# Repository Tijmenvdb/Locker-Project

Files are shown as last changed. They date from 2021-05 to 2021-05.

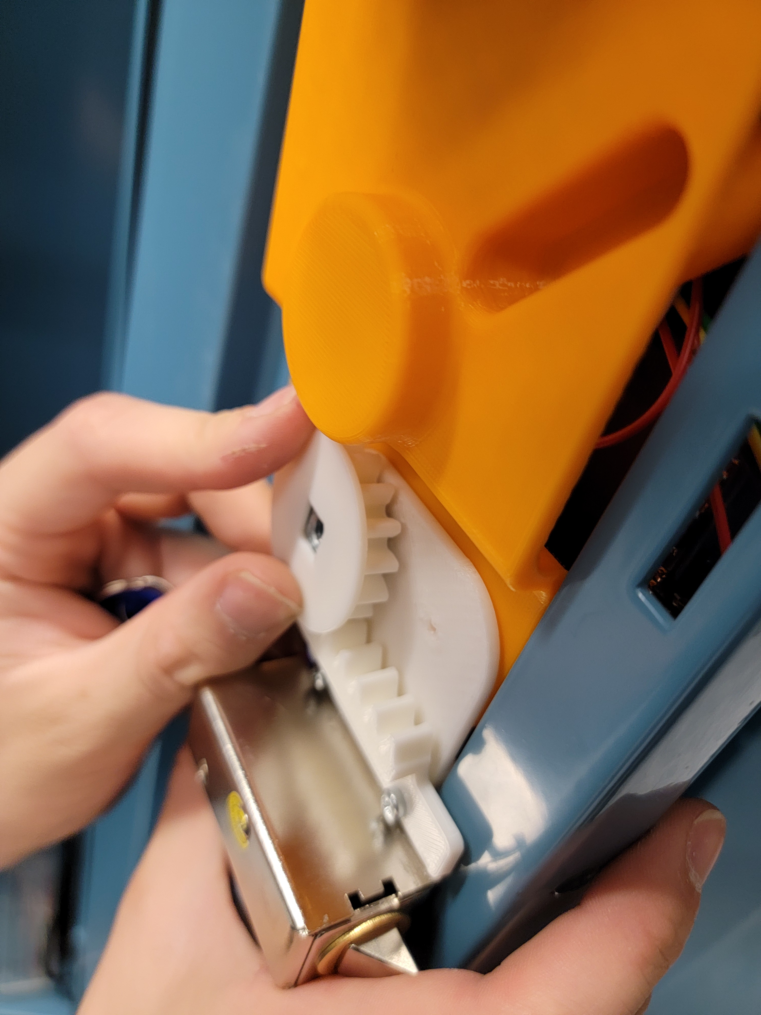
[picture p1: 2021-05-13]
CSE453 Project/Locker Documentation/Images/Assembly Pictures/20210508_183917.jpg

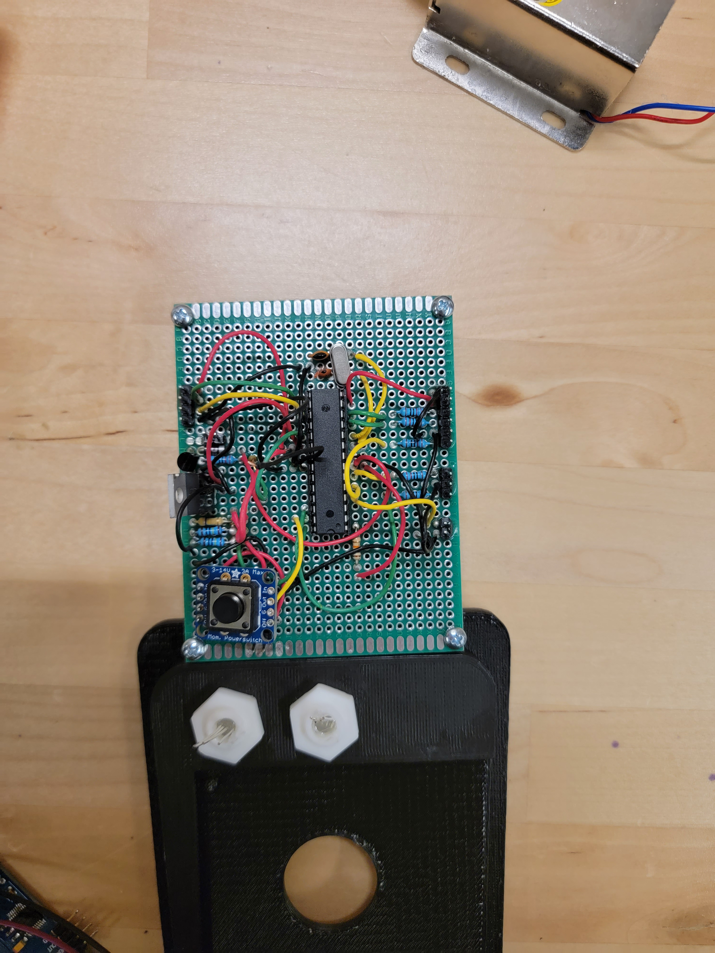
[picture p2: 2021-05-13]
CSE453 Project/Locker Documentation/Images/Assembly Pictures/20210508_151816.jpg

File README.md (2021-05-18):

# Locker-Project
We created three lockers, two for Depew Middle school and one for Alden High school. The Depew lockers we created for kids who have trouble opening up there lockers. The Alden Locker is a prototype locker for there school. We used the same hardware design for all the lockers and different code between Depew and Alden because they had different needs.

The Depew High School locker project focuses on customized lockers for individuals with physical disability. According to the needs of the client, each lock has to be designed specifically for each user to solve their problem with accessing the locker independently. Our locker is to help a student with physical or visual impairments so that they can operate the lockers without any trouble.

The Alden locker was designed as an automated and easily operated locker for Alden High School. According to the staff at Alden High School, the current lockers have frequent locker jams. This results in additional custodial resources which can be prevented by having better designed lockers.

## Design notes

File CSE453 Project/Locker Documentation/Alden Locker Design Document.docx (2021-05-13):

Automated Locker

Design Document

Prepared for:

Alden High School

Prepared By:

Tijmen Van Der Beek, Miren Patel, Siquan Wang, Xiaoang Zhang, Dazhou Liu

School of Engineering and Applied Sciences

University at Buffalo, The State University of New York

Spring 2021

Table of Contents

Introduction 2

Note for RFID and NFC Components 2

RFID Locker Module 2

Software 2

Important Static Variables 3

Functions 3

Interrupts 3

Main Flow Chart 4

RGB LED Indicator Key 5

Status LED (LEFT) 5

Battery LED (RIGHT) 6

Schematic 7

Description 7

Parts List 8

Case 9

Front 9

Inside Front 9

Back 10

Inside Back 11

Mechanical Design 11

Upgrades 12

Troubleshooting 12

References 13

# Introduction

The purpose of this project is to design an automated and easily operated locker for Alden High School. According to the staff at Alden High School, the current lockers have frequent locker jams. This results in additional custodial resources which can be prevented by having better designed lockers. These RFID Locker Modules will use Radio Frequency Identification (RFID) for authentication for opening the lockers by both registered students as well as administrative personnel such as the custodial staff. The design will also ensure that the lock mechanism does not have frequent locker jams. For the safety and security of the school, a mechanical override system will also be incorporated to allow for the circumvention of the digital systems. Due to the potential for a large rollout of this system, scalability and reliability have been key considerations at every step of our development. Everything can be found on Github (https://github.com/Tijmenvdb/Locker-Project).

# Note for RFID and NFC Components

The locking/unlocking mechanism is executed by RFID components in our design. However, the previous locker team working on Alden High School locker chose to use the NFC components. In the spring 2021 semester, we acquired the NFC components and attempted to implement them. The result was that the NFC components did not work as expected due to improper factory functionalities. As a consequence, we decided to use RFID modules to lock/unlock the locker in Alden High School.

# RFID Locker Module

1. Master tag: Acts as a master key, allowing opening the lock mechanism on any locker.
2. Registrar tag: Puts the locker into registration mode, allowing for registration of a new student tag. Student tag registrations persist until cleared with the clear tag.
3. Clear tag: Clears all registered student tags. Only master tags can open the locker until a new student tag is registered.
4. Reset Button: When the locker is first booted up you can register the administrative tags after that the reset button is the only way to reset the locker and re-register new ones.

The use of administrative tags in this way eliminates the need for additional input channels (such as buttons), reducing the hardware complexity and cost. We have also attempted to minimize the number of output channels as well, using a single RGB LED to convey the system state.

# Software

The provided RFID Locker Module software is written in C++ for deployment on an Arduino Uno (or equivalent). The main source code is LockerCodeAlden.ino. In the source code (available on our Github (https://github.com/Tijmenvdb/Locker-Project) repository) you’ll find descriptive comments to help with understanding the code’s functionality as well as its deployment.

## Important Static Variables

- Init_num: This is the number it checks to see if it has been initialized yet.
- tagDelay: This is the processing delay between each tag read in ms
- ERRORBlinkRate: This is the speed at which the led binks in ms
- LOCKER_TIME: 30 This is the time the locker has till it turns off in sec when locked
- UNLOCK_TIME: 10 This is the time the locker will be unlocked for in sec when unlocked

## Functions

- void ReadSerial(String &ReadTagString): This function reads the tag in front of the RFID sensor and passes the string through ReadTagString
- void clearTags(): This function clears all the student tags in EEPROM
- void resetLocker(): Resets the locker
- void loadTags(): This function loads all the tags from the EEPROM into the global tag_list
- bool writeTag(String data): This function adds a tag to memory and returns true if successful and false if reached max tags
- int checkTag(String data): Checks the given tag with the registered tags if any of them match it returns int for the type of tag.
- void setLed (int rVal, int gVal, int bVal): Sets the rgb led color of only the status LED
- void ledBlink (int rVal, int gVal, int bVal, int halfCycle, int blinkCount): Blink the RGB LED given the provided RGB value, the time for each half cycle (time off, time on, in ms) and the number of blinks. (Only Status LED)
- void soundFeedback(int type): Adds sound effects to the locker for better feedback (0 start, 1 unlock, 2 wrong tag)
- void initLocker(): Initializes the locker with faculty tags only runs if not initialized
- void setBatteryLed(): Sets the battery led color based on the voltage of the battery
- void enableTimerInterrupt(): Sets the timer interrupt to interrupt every second (We have a counter to determine the time)
- void resetTimer(): Resets the timer counter back to Locker_Time whenever called

## Interrupts

- void resetISR(): Sets reset to true and sets led to purple
- ISR(TIMER1_COMPA_vect): Turns off locker after timer interrupt activates and counter is at 0

# Main Flow Chart

This is a flow chart of the logic that the locker should follow.

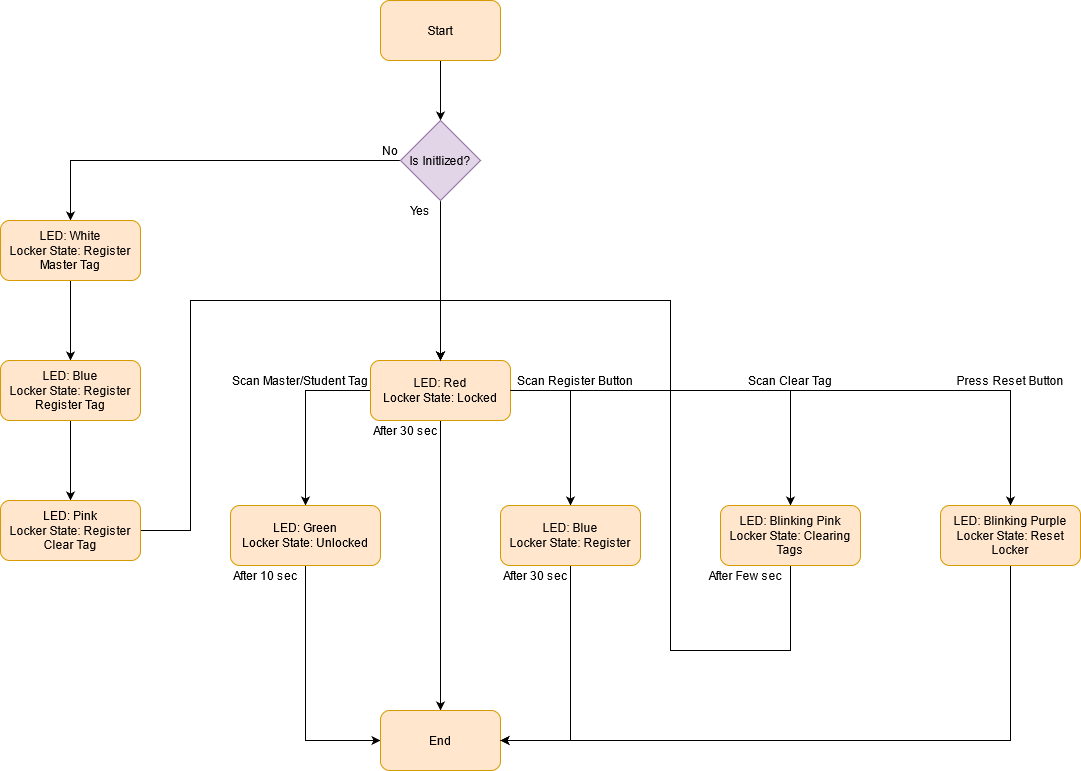
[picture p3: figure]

# RGB LED Indicator Key

## Status LED (LEFT)

State | LED Color
Initial State | OFF
Locked | RED
Unlocked | Green
Processing | Yellow
Register Mode | Blue
If the tag is wrong | Blinks RED
If the tag is correct | Blinks GREEN
Successful Register | Blinks Blue Twice
Already Registered | Blinks Blue Three Times
Unsuccessful Register | Blinks Red
Already Registered Faculty Tag | Blinks Red and color of tag type.
Resets Locker | Blinks Purple turns off
Master Tag Registration Mode | White
Register Tag Registration Mode (Only after Master Tag Reg) | Blue
Clear Tag Registration Mode | Pink
Successful Faculty Tag Registration | Blinks Color of tag type

## Battery LED (RIGHT)

State | LED 2 Color Battery Indicator LED
Initial State | OFF
When the push button is pressed, it turns on the circuit and is ready to read the tags. | GREEN: if the battery level is sufficient (battery is greater than 10 V) RED: if the battery is at low level (the battery is less than 8 V but greater than 7 V) Blinking RED: if the battery is low (the battery is less than 7 V). At this point the circuit won’t turn on, battery recharge is necessary
OFF State | OFF

# Schematic

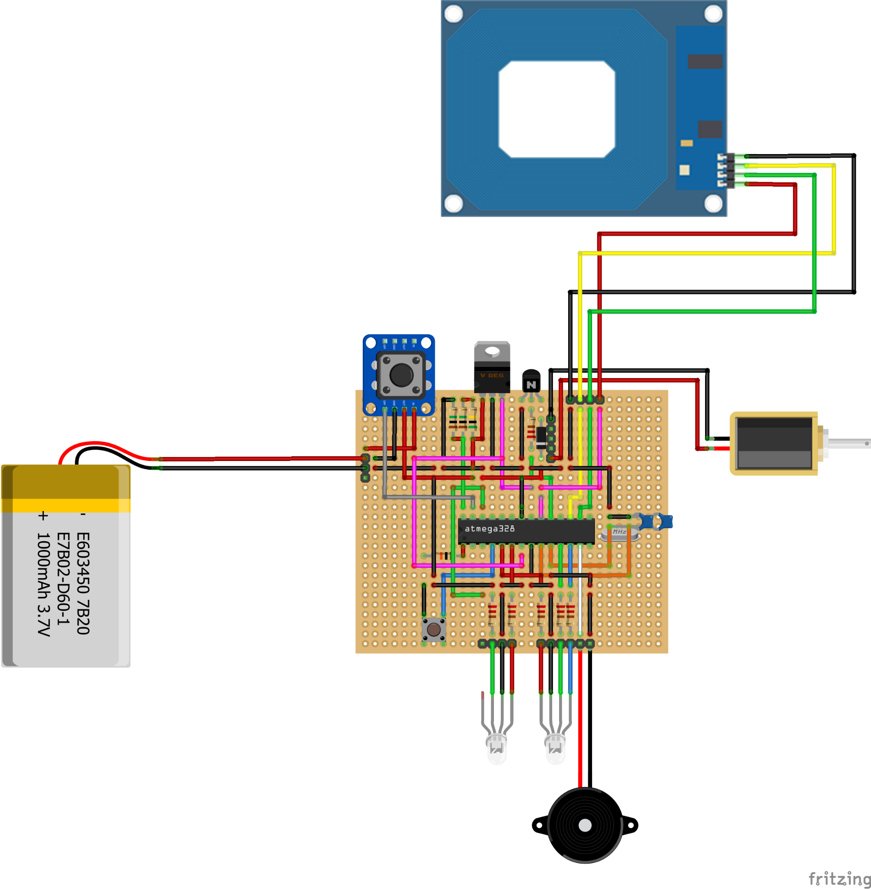
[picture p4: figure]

## Description

- We are using the atmega328p Chip that we program with the arduino and put on our circuit.
- The battery is a 12 3Ah Dewalt battery. The one in the schematic is a placeholder image.
- Adafruit Power Switch Button: This is the power button for the locker with an off pin on it allowing us to turn off the locker after being idle for a certain amount of time.
- The voltage divider takes the 12 volt power line and reduces it so the chip can read it and set the Power Led appropriately. The voltage divider consists of two 1M Ohms, one 470k Ohm and the output voltage shouldn’t exceed 5 volts.
- The Voltage regulator brings down the 12 volt to 5 volt to power the chip and RFID reader.
- The 2N2222 Transistor is used to power the solenoid with the chip.
- Status RGB LED:
  - Red On, but locked
  - Green→ Unlocked
  - Blue→ Register mode
  - Blinking pink→ Clearing all tags
  - Blinking blue→ Successful tag registration
- Power RGB LED:
  - Red Low Battery
  - Green High Battery
  - Blinking Red Out of Power
- We are using headers on the circuit board so parts can be easily replaced.
- We are using 2 22pF capacitors and a 16Mz Clock to run the chip.
- We have a 10k Ohm resistor on the reset pin on the chip.
- The resistors on the LEDs and 2N2222 transistor are 220 Ohms.

# Parts List

1. Arduino UNO R3 (https://www.mouser.com/ProductDetail/Arduino/A000066?qs=BC3YYPaifMrIue9b%252BHtKQg%3D%3D)
2. Atmega328 chips (https://www.mouser.com/ProductDetail/Microchip-Technology-Atmel/ATMEGA328P-PU?qs=K8BHR703ZXguOQv3sKbWcg%3D%3D) (Remove from Arduino board) (https://www.mouser.com/ProductDetail/Microchip-Technology-Atmel/ATMEGA328P-PU?qs=K8BHR703ZXguOQv3sKbWcg%3D%3D)
3. Adafruit Push-button Power Switch Breakout (https://www.adafruit.com/product/1400)
4. RFID Card Reader - Serial (https://www.mouser.com/ProductDetail/Parallax/28140?qs=sGAEpiMZZMuVJC7Vq%252BMl5ylqeJ96bWxk)
5. RFID Tags (https://www.mouser.com/ProductDetail/Parallax/28161?qs=6siQ5y5nVCyh2S897wNmIQ%3D%3D) x5
6. Diode Rectifier 1N4001 (https://www.sparkfun.com/products/8589) x3
7. Voltage Regulator (https://www.mouser.com/ProductDetail/STMicroelectronics/L7805ABV?qs=xv3lWMc77RfDowMbrj6NxQ%3D%3D&mgh=1)
8. 2N2222A Transistor (https://www.amazon.com/gp/product/B083TNXLHD/ref=ppx_yo_dt_b_asin_title_o08_s00?ie=UTF8&psc=1) x3
9. LED RGB Diffused (https://www.mouser.com/ProductDetail/Kingbright/WP154A4SEJ3VBDZGW-CA?qs=YCa%2FAAYMW01xRqZww6UuiQ%3D%3D) x6
10. 220ohm Resistor (https://www.amazon.com/McIgIcM-resistor-Electronics-resistors-assortment/dp/B06WRQS97C?hvadid=312303208923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) x20
11. 1M ohm Resistor (https://www.amazon.com/McIgIcM-resistor-Electronics-resistors-assortment/dp/B06WRQS97C?hvadid=312303208923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) x2
12. 470k ohm Resistor (https://www.amazon.com/McIgIcM-resistor-Electronics-resistors-assortment/dp/B06WRQS97C?hvadid=312303208923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) x
13. 10k Resistor (https://www.amazon.com/McIgIcM-resistor-Electronics-resistors-assortment/dp/B06WRQS97C?hvadid=312303208923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)
14. 22pf Capacitors (https://www.amazon.com/gp/product/B08LK8DQKF/ref=ppx_yo_dt_b_asin_title_o03_s00?ie=UTF8&psc=1) x2
15. 16Mz Clock (https://www.amazon.com/Uxcell-a14050500ux0216-HC-49S-Crystal-Oscillator/dp/B00NQ82OM0?s=industrial)
16. DeWalt 12v Lithium Ion Battery (https://www.lowes.com/pd/DEWALT-12-Volt-Max-3-Amp-Hours-Lithium-Power-Tool-Battery/1001001766?AID=11554726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)
17. DeWalt 12v-20v Lithium Ion Battery Charger (https://www.amazon.com/dp/B01BQM1A2W?ascsubtag=wtbs_5de7f7eb958a7501630f809d&m=ATVPDKIKX0DER)
18. 5V 2 Terminals Buzzer (https://www.amazon.com/gp/product/B01GJLE5BS/ref=ppx_yo_dt_b_asin_title_o02_s00?ie=UTF8&psc=1) x2
19. Key Lock (https://www.amazon.com/Prime-Line-Products-9945-Drawer-Cabinet/dp/B000BDB686)
20. Solenoid (https://www.mouser.com/ProductDetail/Adafruit/1512/)
21. PCBs (https://www.amazon.com/gp/product/B07FK49T55/ref=ppx_yo_dt_b_asin_title_o05_s00?ie=UTF8&psc=1)
22. White Filament (https://www.amazon.com/gp/product/B06XR7621X/ref=ppx_yo_dt_b_asin_title_o01_s00?ie=UTF8&psc=1) (Used for LED caps)
23. Breadboard, wiring, washers/nuts/screws
24. Push Button (https://www.amazon.com/EG-STARTS-Illuminated-Buttons-Raspberry/dp/B01N11BDX9) (Activation)
25. Push Button (https://www.amazon.com/DAOKI-Miniature-Momentary-Tactile-Quality/dp/B01CGMP9GY) (Reset)
26. Magnetic Push Latches (https://www.amazon.com/gp/product/B07TS2LMHS/ref=ppx_yo_dt_b_asin_title_o09_s00?ie=UTF8&psc=1) (Optional)

# Case

## Front

The front of the case has two LEDs, the power button and the lock for the mechanical override.

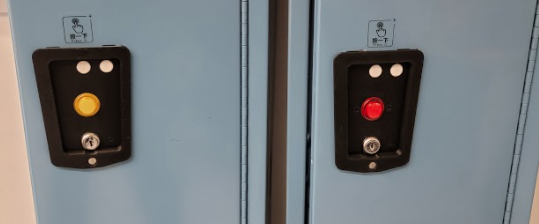
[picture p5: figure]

## Inside Front

The inside shows the RFID reader in the center with the button going through it. We glued the speaker in the bottom corner. We have 2 LED caps screwed in with nuts above the RFID reader. On the top is where we screwed the circuit board. On the bottom is where the lock core goes.

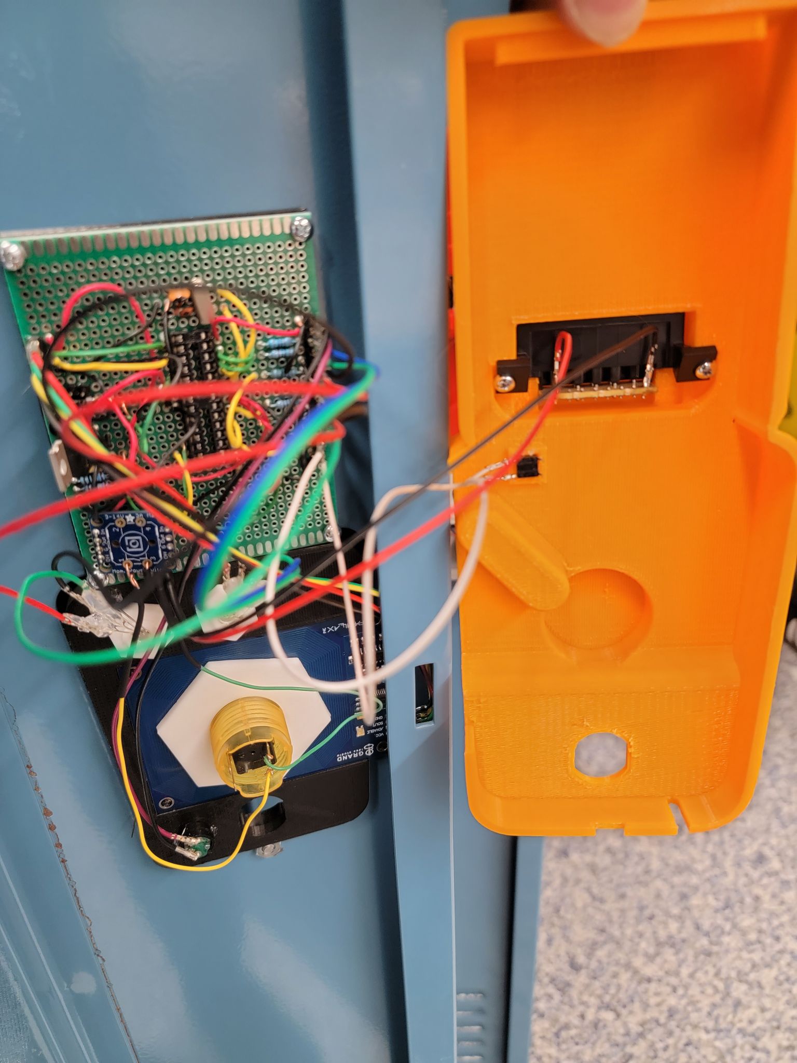
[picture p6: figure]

## Back

We have the spot for the dewalt battery and the register/clear button below that. The register/clear button is recessed so that it can’t be accidentally pressed and must be pushed with something like a pencil.

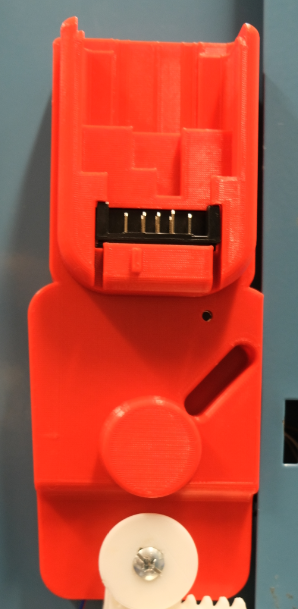
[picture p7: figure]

## Inside Back

We used the charging insert from the dewalt charger and screwed it into the locker case. We glued the register/clear button to the back. The prints can be found on Github (https://github.com/Tijmenvdb/Locker-Project).

# Mechanical Design

The mechanical override utilizes a locker gear and a key gear to horizontally slide the solenoid. The locker gear is a jagged rectangle plate that mounts the solenoid with screw holes. The key gear is screwed to the locker core and is attached to the locker gear.

When a key is inserted into the keyhole and turned, the key gear inside is turned around. As a result, the locker gear with the solenoid screwed to it is slided back and forth. When the solenoid is moved far enough, the solenoid no longer acts as a door latch so that the locker door is unlocked. With the spring mechanism the door must be pushed in before turning the key. The friction of the spring on the solenoid causes the solenoid to move properly. All the 3d parts can be found on our Github (https://github.com/Tijmenvdb/Locker-Project).

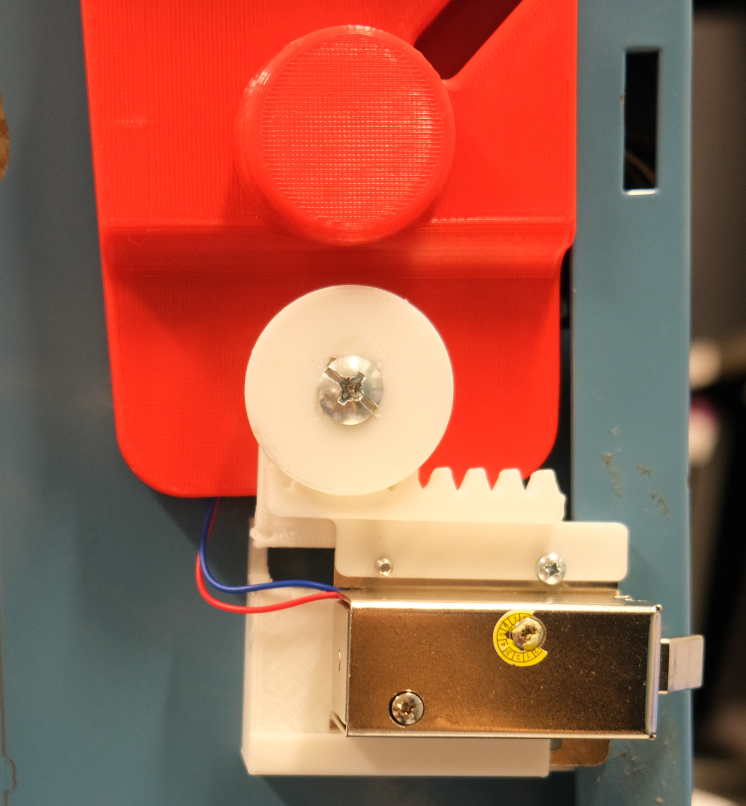
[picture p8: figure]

# Upgrades

- Improving the mechanical override with compact gear built with better materials to improve smoothness of unlocking process or changing the whole design to a superior one when the solenoid can be properly mounted.
- Custom manufactured circuit board instead of hand soldering through-hole board to improve stability and durability of the lock and speed up the soldering process.
- Some improvements to the case and overall design of the locker to make it more durable.
- Designing a better case to incorporate better with the school locker with the schools latch design.
- Central power distribution system to multiple lockers and put lockers in parallel.
- Incorporate a larger battery like the 20v 10Ah dewalt battery.
- Better energy efficiency.
- Disable the access of the reset button for normal users. Only the administrators should have access to it.
- See what issues the current prototype comes up with during testing and improve from there.

# Troubleshooting

- The circuit will not turn on properly at all if without the RFID reader attached to it.
- If the circuit is not working properly or not turning on try replacing the chip.
- If the circuit turns on but the startup sound sounds off clear all the tags with the button on the back. (This will most likely happen with a new chip that was just programed)
- If the circuit turns on at 7v input instead of 12v input or is not turning on at all, the voltage regulator might be damaged. Swap a new voltage regulator to fix the problem.
- If the status LED is blinking in red color while being powered by 12v, the voltage divider might be broken. Desoldering the 3 resistors and resoldering on 3 new resistors with the same resistance should fix this issue.
- If solenoid is not working, this could be either the solenoid or the npn transistor. Swap the solenoid first and test the functionality. If still not working, swap the npn transistor on board.
- If any plastic part is broken, you can reprint the part and replace the broken part.
- If the locker does not read the tags, clear all the tag registration and try to re-register one tag. If still not functioning, check the RFID wire connection with the board and retry. If still having trouble, replace the RFID with a new one. If the problem still persists after these steps, replace the processing chip on the board with a new one.
- If the buzzer does not work, check the wire connection with the board first and retry. If still having trouble, replace the buzzer with a new one.

# References

We inherit the previous 2 locker teams ideas then improve and expand from them. This is their Github1 (https://github.com/shellshocker98/CSE453-Locker-Project) Github2 (https://github.com/DonBrant/CSE-453-ALB/tree/develop).

Our Github (https://github.com/Tijmenvdb/Locker-Project).

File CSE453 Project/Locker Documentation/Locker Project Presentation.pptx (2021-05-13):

## Locker Project

Team Members:
Tijmen Van Der Beek
Miren Patel
Siquan Wang
Xiaoang Zhang
Dazhou Liu

## Introduction

- The Depew High School locker project focuses on customized lockers for individuals with physical disability. According to the needs of the client, each lock has to be designed specifically for each user to solve their problem with accessing the locker independently.
- The purpose of the Alden High School Locker is to design an automated and easily operated locker for Alden High School. The locker we designed is a prototype and the idea is that they can run multiple of them off of one battery.

## Alden Flowchart


## Depew Flowchart

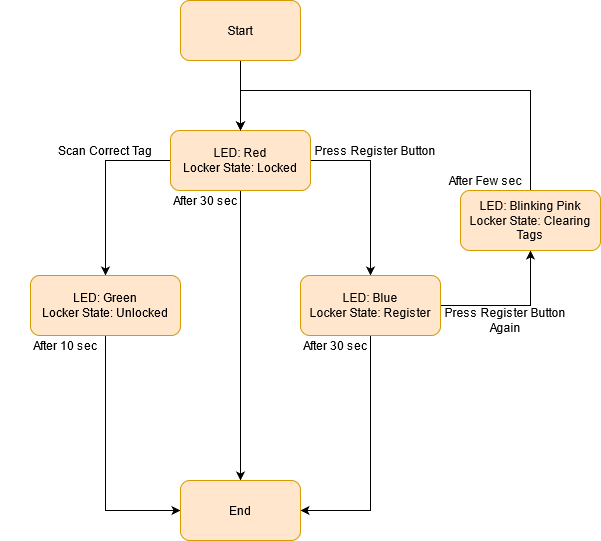
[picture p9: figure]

## Schematic

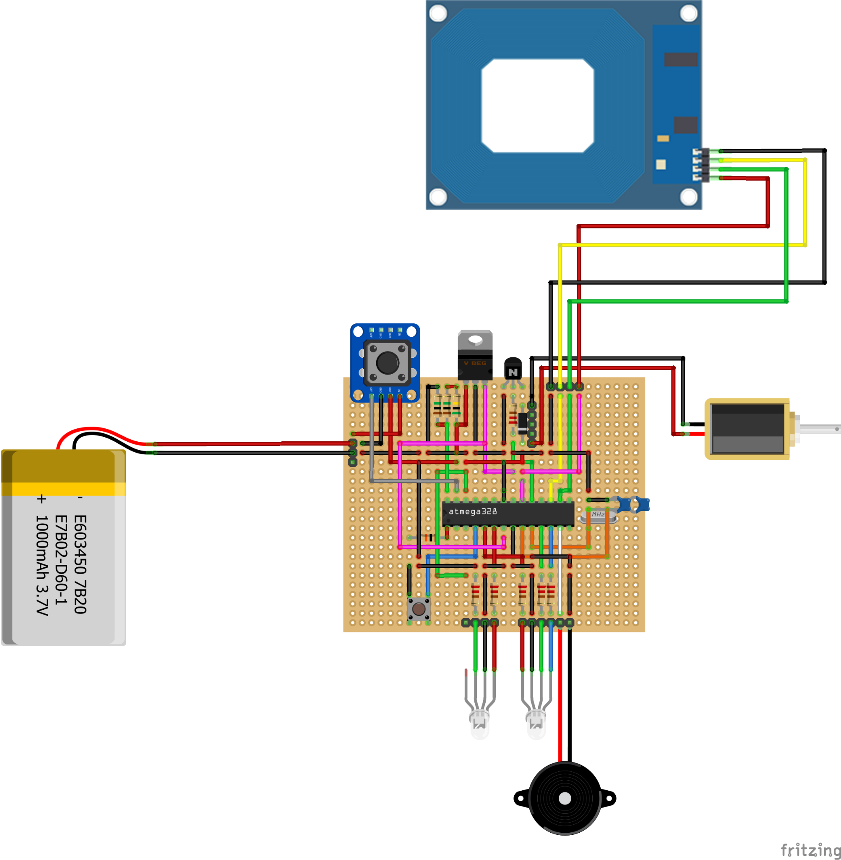
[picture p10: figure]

Major Components:
- DeWalt 12v Lithium Ion Battery
- RFID Card Reader
- Solenoid
- 5V 2 Terminals Buzzer

## Case Outside

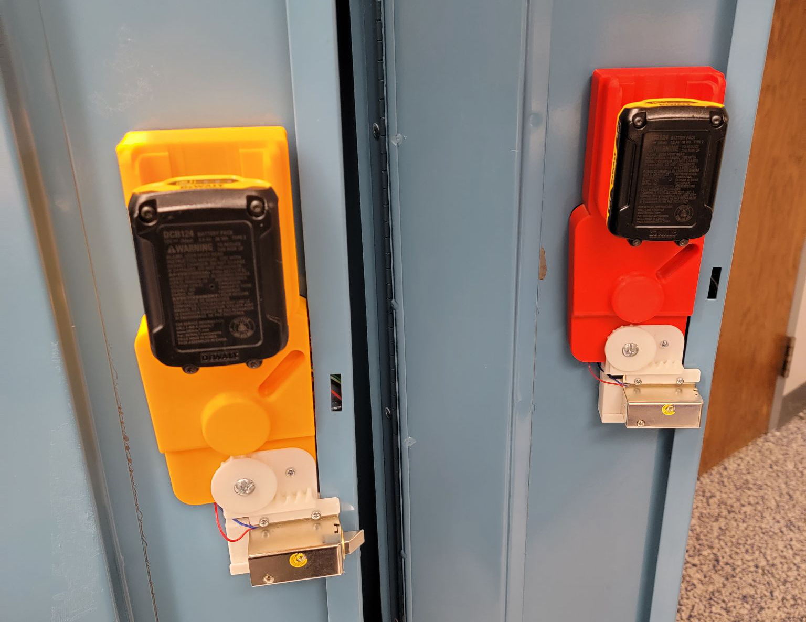
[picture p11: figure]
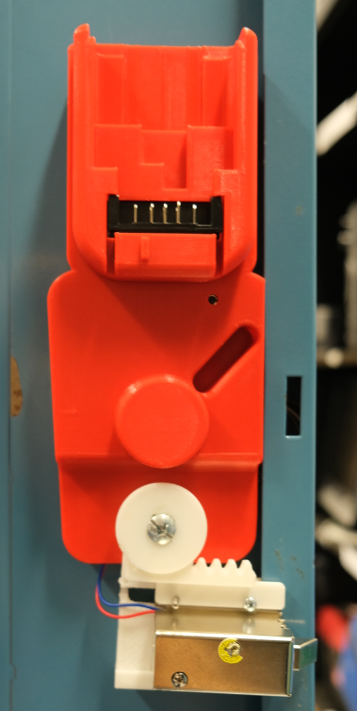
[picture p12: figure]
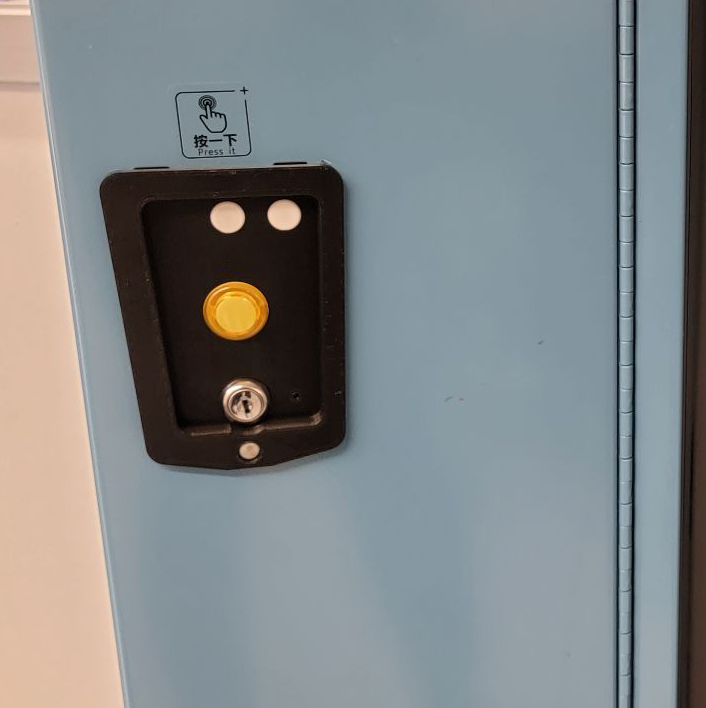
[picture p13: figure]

## Case Inside

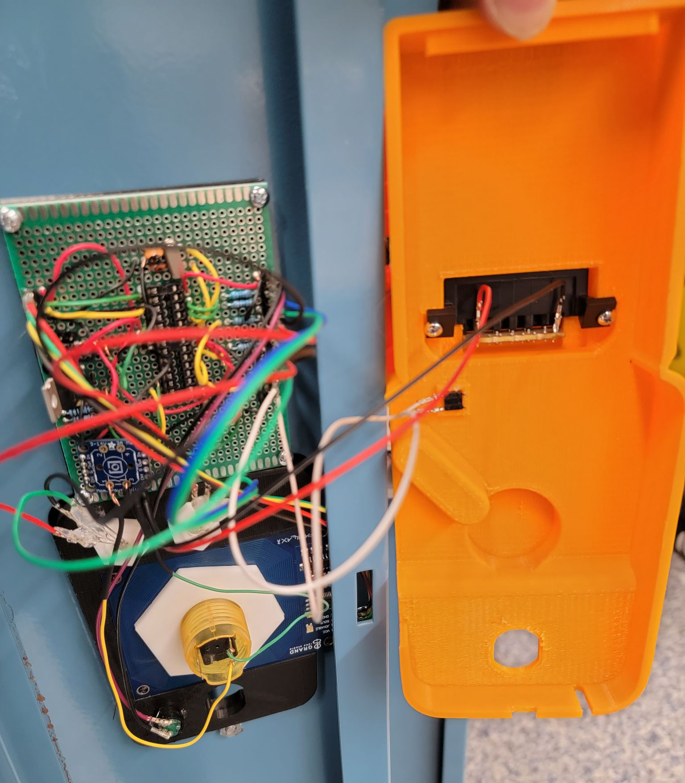
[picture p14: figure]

## Mechanical Override

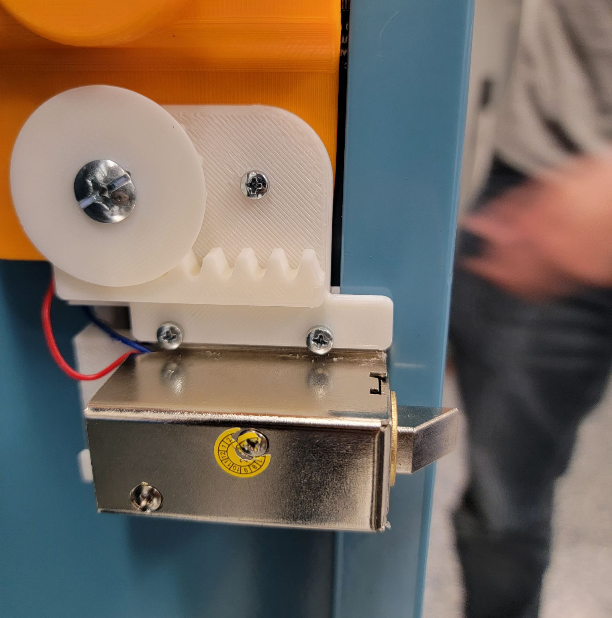
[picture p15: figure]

We used a gear and rack to move the solenoid horizontally for achieving the manual override feature.

## Depew Locker Spring

We install a magnetic push latch for each locker. This latch push open the door automatically once unlock.

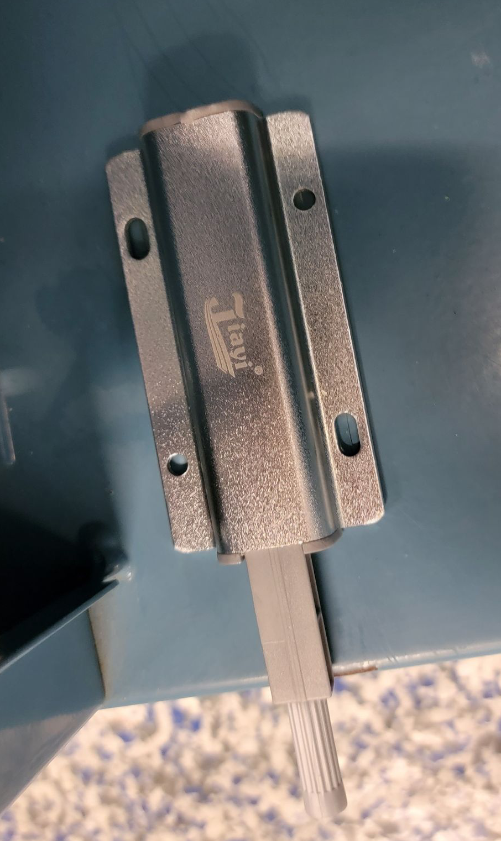
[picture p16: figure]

## Possible Upgrades

- Improve Mechanical Override
- Manufactured Circuit Board
- Improve some parts of the case
- Design a case that works with the Alden Latch
- Design it with a bigger battery like 20v Dewalt
- Disable reset button to Students
- Put multiple lockers in parallel with one battery
- Improve on issues that come up during testing
- Improve energy efficiency

## Demo

- Open (Outside View):
- Open (Inside View):
- Register & Clearing :
- Mechanical Override:

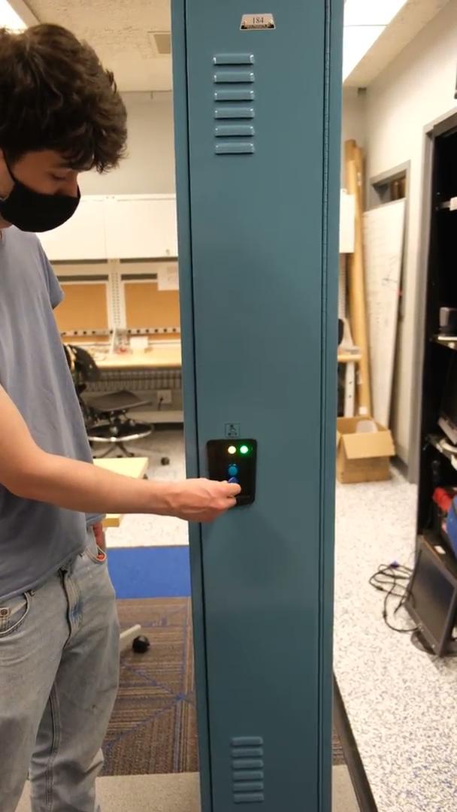
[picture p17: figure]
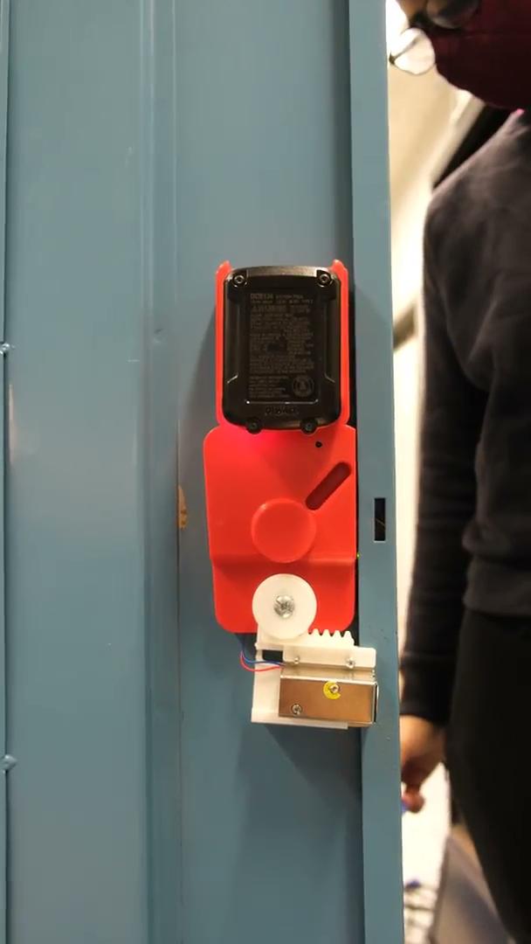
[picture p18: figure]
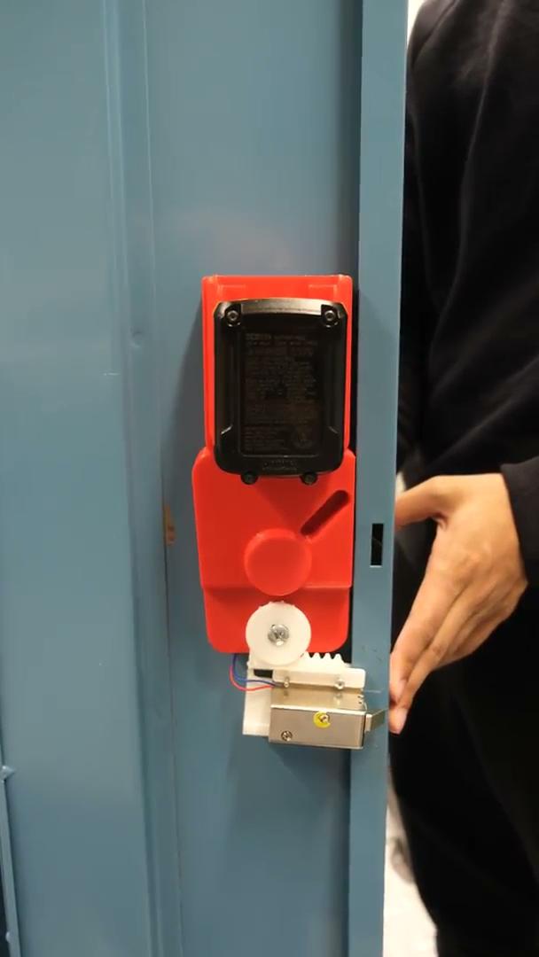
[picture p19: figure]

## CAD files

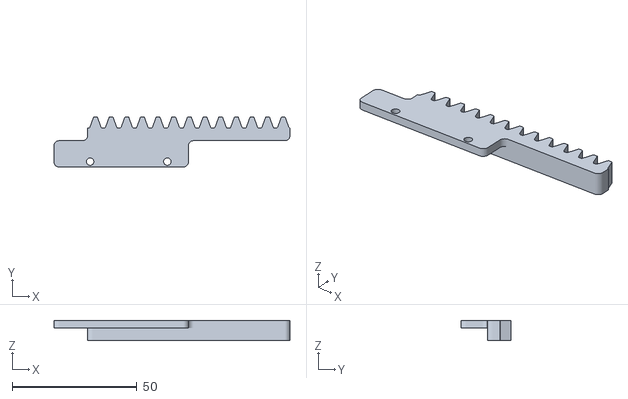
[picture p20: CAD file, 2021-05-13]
CSE453 Project/Locker STL Files/SolenoidRack(L).stl
94.8 x 20.0 x 8.17

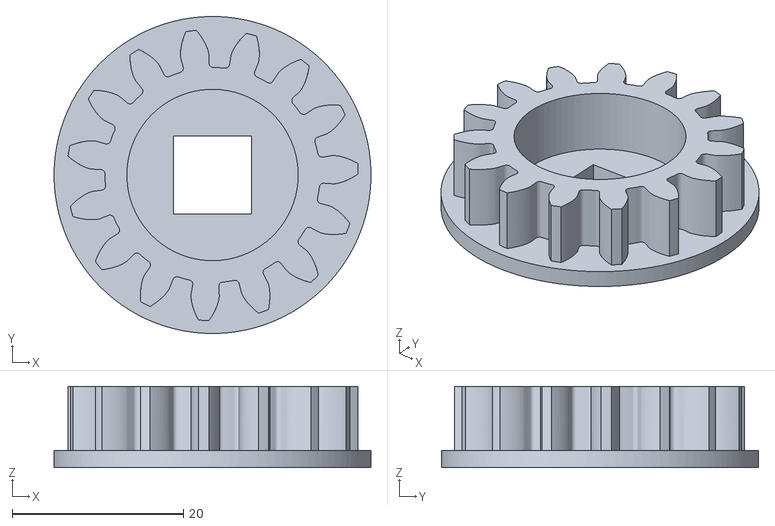
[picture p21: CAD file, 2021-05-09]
CSE453 Project/Locker STL Files/SolenoidGear.stl
37.0 x 37.0 x 9.47

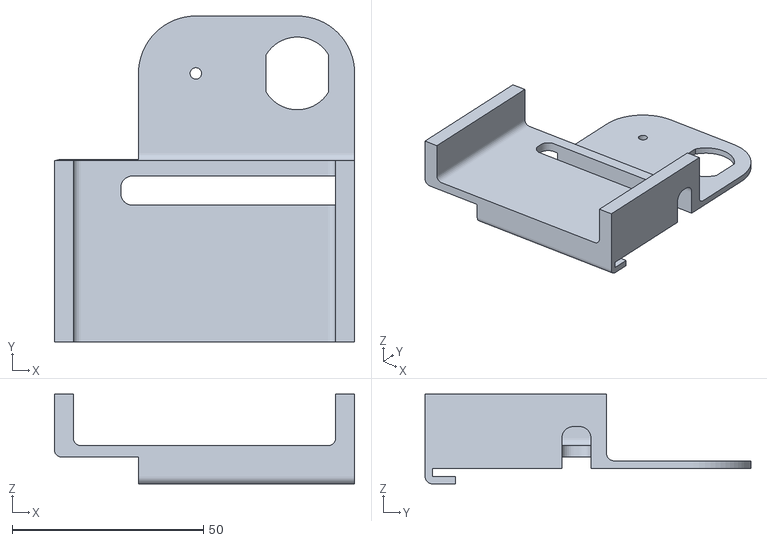
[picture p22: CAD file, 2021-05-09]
CSE453 Project/Locker STL Files/SolenoidMount.stl
78.5 x 85.2 x 23.5

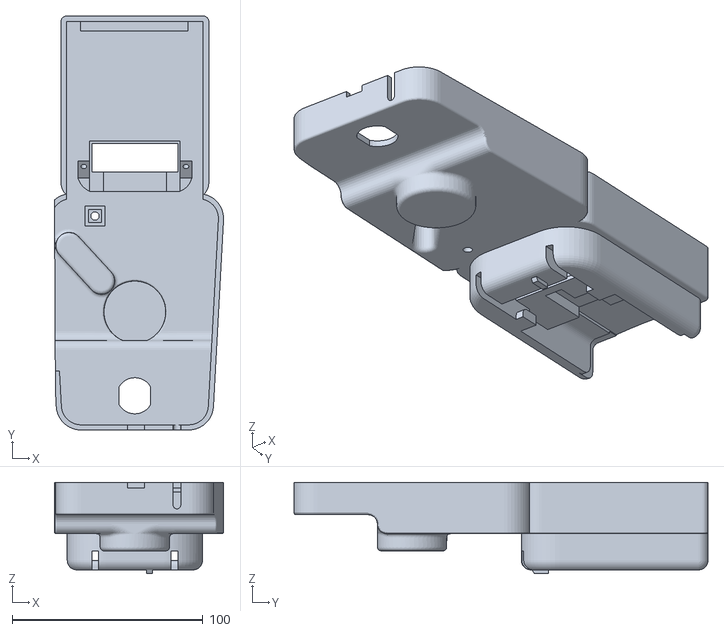
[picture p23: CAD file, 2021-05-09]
CSE453 Project/Locker STL Files/Case_Back.stl
88.7 x 217.3 x 48.0

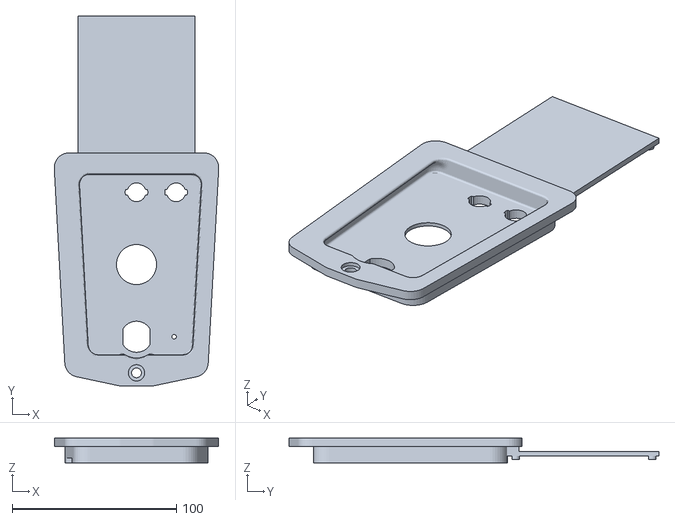
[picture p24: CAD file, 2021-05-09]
CSE453 Project/Locker STL Files/Case_Front.stl
100.2 x 225.4 x 15.0

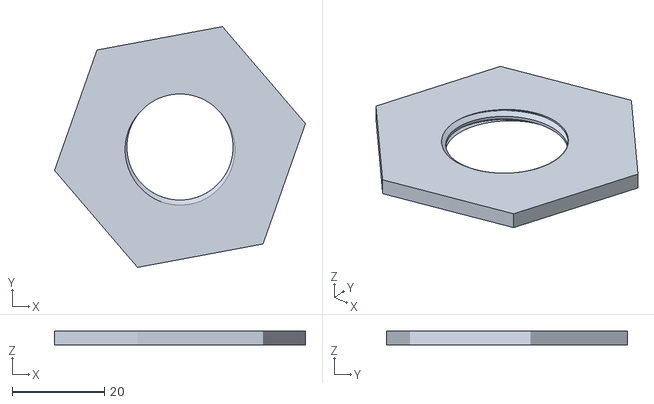
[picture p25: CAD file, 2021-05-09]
CSE453 Project/Locker STL Files/ButtonNut.stl
54.5 x 52.3 x 3.00

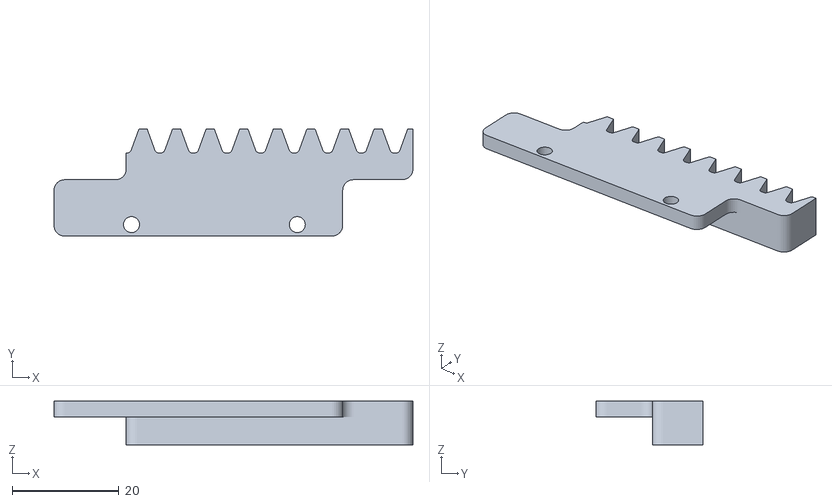
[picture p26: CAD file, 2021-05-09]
CSE453 Project/Locker STL Files/SolenoidRack.stl
67.1 x 20.0 x 8.17

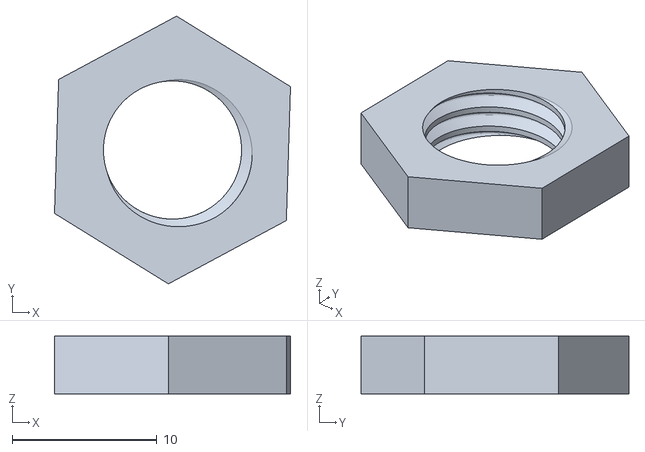
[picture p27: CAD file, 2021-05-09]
CSE453 Project/Locker STL Files/LedNut.stl
16.3 x 18.5 x 4.00

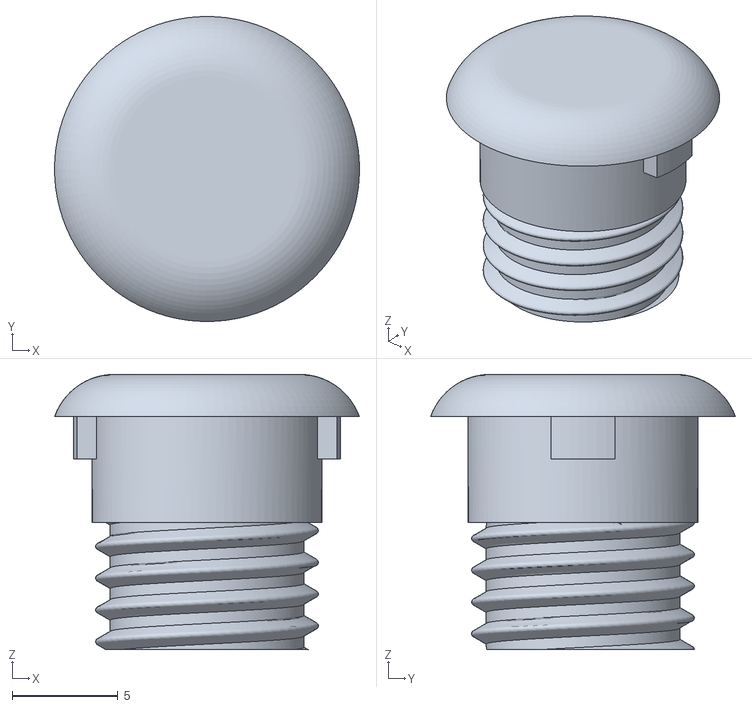
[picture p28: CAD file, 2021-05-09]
CSE453 Project/Locker STL Files/LedCap.stl
14.4 x 14.4 x 13.0

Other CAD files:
CSE453 Project/Locker Fusion 360 Files/Rack and Gear (For creating a rack and gear).f3d

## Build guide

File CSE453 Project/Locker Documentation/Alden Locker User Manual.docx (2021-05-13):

USER MANUAL FOR AUTOMATED LOCKER BANK IN ALDEN HIGH SCHOOL

Prepared By:

Tijmen Van Der Beek, Siquan Wang, Miren Patel, Xiaoang Zhang, Dazhou Liu

School of Engineering and Applied Sciences

University at Buffalo, The State University of New York

Spring 2021

Contents

1 Introduction 2

2 Locker Usage 2

2.1 Locker Activation 2

2.2 Unlocking 2

2.3 Locking 2

2.4 Clearing Student Tags 3

2.5 Registering Student Tags 3

2.6 Initializing Locker 3

2.7 Resetting Locker Tags 3

3 LED Status 4

4 RFID Tags 5

5 Speaker Sounds 5

6 Mechanical Override 5

7 Power Source 6

8 Troubleshootings 6

9 Safety Information 6

# 1 Introduction

Based on client feedback, the locker system is designed to reduce frequent locker jams imposed by the current locker in Alden High School. In addition, features aiming to allow mass production of this locker system are incorporated. By using designated tags for the locker, users have an option for operating their locker with simplicity.

To facilitate the user to transit to this new locker system, this user manual includes descriptions of the electronic components, procedures of using the locker system and troubleshootings for possible failures. Photos of system components are also included to make this user manual intuitive.

# 2 Locker Usage

## 2.1 Locker Activation

Pressing the button on the front panel of the locker door activates the locker system. A LED enclosed inside the locker door then becomes red to indicate that the locker is ready to read tags but is locked. A speaker also produces sound to indicate this status. If the locker is idle for 30 seconds it will turn off automatically.

## 2.2 Unlocking

To unlock, an authorized RFID tag must be scanned on the front panel. They are master and user tags. When a master or an authorized user tag is detected, the locker door unlocks. The LED’s color turns to green and the speaker produces a sound. At this point, the user needs to push the locker door. Then the locker door pops out automatically, and the user gains access to their stuff in the locker.

## 2.3 Locking

If no action is taken by the user after 10 seconds upon unlocking, the solenoid will automatically lock. Then the user needs to lock the locker door again by pressing it back to the initial position. You can also press the button again to lock the locker earlier.

## 2.4 Clearing Student Tags

To clear all the student tags just scan the clear tag, the LED will blink pink and all student tags will be removed.

## 2.5 Registering Student Tags

To register a student tag scan the register tag. When the LED turns blue scan the student tag you want to register. If it blinks blue it has successfully registered if red then there was an issue.

## 2.6 Initializing Locker

When the locker is first turned on or reset it will start up in initialization mode. In this mode the led starts white and is trying to register the faculty tags. You start by choosing the master tag for the locker. Next it will turn Blue for the register tag. Next pink for the clear tag. Once all faculty tags are registered the locker will start up normally.

## 2.7 Resetting Locker Tags

If you are missing one of the faculty tags for your locker you will have to reset the locker to put the locker back in initialization mode. To reset the locker press the button (lightly) on the back of the case with a pencil. The led will blink purple twice and turn off when the button is pressed it will be in Initialization Mode.

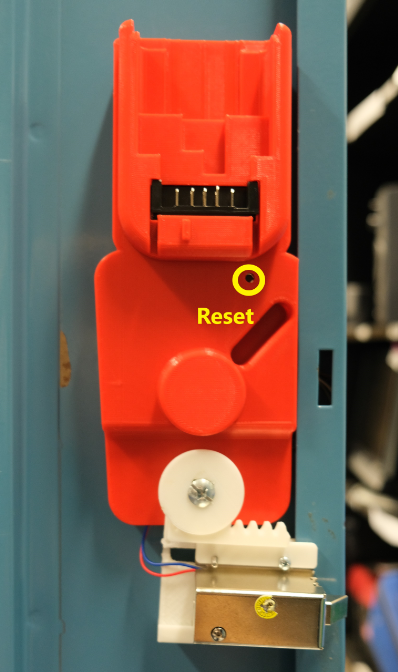
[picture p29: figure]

# 3 LED Status

There are two LEDs on the front panel.

- The left LED (right above the push button) indicates the status of the locker.

LED Colors | Locker Status
Off | Initial Status
Red | Push button pressed, circuit turned on and ready to read the tags.
Green | Unlocked
Blue | Register mode or Register tag registration mode (after master tag reg)
Yellow | Processing
Pink | Clear tag registration mode
White | Master tag registration mode
Blinking RED | Wrong tag detected or Unsuccessful register
Blinking RED and Color of Tag Type | Faculty tag already registered
Blinking Green | Correct tag unlocking
Blinking Blue Twice | Successful tag register
Blinking Blue Three Times | Already registered
Blinking Pink | Clearing all tags
Blinking Purple and Turns Off | Locker reset

- The right LED indicates the voltage level of the DeWalt battery.

LED Colors | Battery Status
GREEN | Battery level sufficient (battery voltage greater than 10V)
RED | Battery is low (battery voltage less than 8V but greater than 7V) The battery needs to be charged.
Blinking Red | Battery is low (battery voltage less than 7 V) At this point, the locker will turn off after blinking red.
Off | Off

# 4 RFID Tags

There are four types of tags: master, register, clear and user tag.

# 5 Speaker Sounds

A speaker is embedded for users with hearing impairment. There are three types of speaker sound.

- Sound when locker initialized
- Sound when unlocked
- Sound when error occured

# 6 Mechanical Override

Mechanical override is a solution to unlock the door for emergency situations (power failure or lost tags). The core components are two gears that are able to slide the solenoid horizontally.

A key is used to unlock externally, and the position of inserting the key is a keyhole located below the red push button on the front panel. When unlocking by mechanical override, the user first must insert the key and turn it clockwise. Upon successful unlocking, the user must turn the key counterclockwise to the initial position so that the locker is locked again.

# 7 Power Source

The power source of each locker is a DeWalt 12V battery, and it does not utilize wall power. When exhausted, the battery inside the locker door needs to be detached and charged in the DeWalt Battery Charger.

By fully charging the DeWalt 12V battery, the locker circuits can be supported for approximately 3 months, assuming each user unlocks five times a day.

In case of power failure of the DeWalt 12V battery, mechanical override is required to unlock the locker for further actions.

# 8 Troubleshootings

- If the locker turns on but doesn't seem to work properly try recharging the battery.
- If the solenoid stops working when the locker is unlocked try recharging the battery.
- If the locker is blinking red or not turning on when pressing the power button try recharging the battery.
- If the locker is not turning on try pushing in the dewalt battery completely.
- If the solenoid latch is stuck in unlock position, easily tab the solenoid case to reset back to lock position.

# 9 Safety Information

Most of the wires and electronic components are enclosed inside cases. But one portion of a wire that connects to the solenoid may be exposed. Be careful to avoid contacting that wire.

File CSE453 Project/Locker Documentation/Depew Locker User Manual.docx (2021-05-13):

USER MANUAL FOR LOCKER WITH SPECIAL NEEDS IN DEPEW HIGH SCHOOL

Prepared By:

Tijmen Van Der Beek, Siquan Wang, Miren Patel, Xiaoang Zhang, Dazhou Liu

School of Engineering and Applied Sciences

University at Buffalo, The State University of New York

Spring 2021

Contents

1 Introduction 2

2 Locker Usage 2

2.1 Locker Activation 2

2.2 Unlocking 2

2.3 Locking 3

2.4 Clearing and Registering Tags 3

3 LED Status 4

4 Speaker Sound Clarifications 5

5 Mechanical Override 5

6 Power Source Manipulation 5

7 Troubleshootings 6

8 Safety Information 6

# 1 Introduction

Based on feedback provided by clients, this electrical locker system is designed with customized functions to assist students having trouble accessing a mechanical locker. By using this locker system, a user (student) is able to gain access to their locker without challenges.

To facilitate users to transit to this new locker system, this user manual includes descriptions of the electronic components, procedures of using the locker system and troubleshootings for possible failures. Photos of system components are also included to make this user manual intuitive.

# 2 Locker Usage

## 2.1 Locker Activation

Pressing the button on the front panel of the locker door activates the locker system. A LED enclosed inside the locker door then becomes red to indicate that the locker is ready to read tags but is locked. A speaker also produces sound to indicate this status. If the locker is idle for 30 seconds it will turn off automatically.

## 2.2 Unlocking

To unlock, an authorized RFID tag must be scanned on the front panel. The LED’s color turns to green and the speaker produces a sound to indicate the unlocking status. At this point, the user needs to push the locker door. Then the locker door pops out automatically, and the user gains access to their stuff in the locker.

## 2.3 Locking

If no action is taken by the user after 10 seconds upon unlocking, the solenoid will automatically lock. Afterwards, the user needs to lock the locker door again by pressing it back to the initial position. You can also press the button again to lock the locker earlier.

## 2.4 Clearing and Registering Tags

To register a tag, first turn on the locker, unlock it if the door is closed. Once the door is open, reactivate the locker in locked mode. Press the button on the inside panel of the locker with a pencil. (Don’t press with too much force) Once the button has been pressed the led will turn blue indicating it is ready to register a tag. Scan the tag you want to register, if the led blinks blue it has registered successfully. You can register up to 32 tags to one locker.

To clear the tags registered to the locker press the button on the back of the locker twice. Once it was pressed the second time the locker led should blink pink twice this indicates that there are no registered tags to the locker. Make sure to register another tag before closing the locker.


# 3 LED Status

There are two LEDs on the front panel.

- The left LED (right above the push button) indicates the status of the locker system.

LED Colors | Locker Status
OFF | Initial Status
RED | Push button pressed, circuit turned on and ready to read the tags.
Blinking RED | Wrong tag detected
GREEN | Unlocked
Blinking Green | Correct Tag unlocking
Blue | Register Mode
Blinking Blue | Successful Tag register
Blinking Pink | Clearing all tags

- The right LED indicates the voltage level of the DeWalt battery.

LED Colors | Battery Status
Initial Status | Off
GREEN | Battery level sufficient (battery voltage greater than 10V)
RED | Battery is low (battery voltage less than 8V but greater than 7V) The battery needs to be charged.
Blinking Red | Battery is low (battery voltage less than 7 V). At this point, the locker will turn off after blinking red.
Off | Off

# 4 Speaker Sound Clarifications

A speaker is embedded to facilitate users with hearing impairment. There are three types of speaker sound, indicating different locker status.

- Sound when locker initialized
- Sound when unlocked
- Sound when error occured

# 5 Mechanical Override

Mechanical override is a solution to unlock the door for emergency situations (power failure or lost tags). The core components are two gears that are able to slide the solenoid horizontally.

A key is used to unlock externally, and the position of inserting the key is a keyhole located below the red push button on the front panel. When unlocking by mechanical override, the user first inserts the key, presses in the locker door and turns it counterclockwise. Upon successful unlocking, the user must turn the key clockwise to the initial position so that the locker is locked again.

# 6 Power Source Manipulation

The power source of each locker is a DeWalt 12V battery, and it does not utilize wall power. When exhausted, the battery inside the locker door needs to be detached and charged in the DeWalt Battery Charger.

By fully charging the DeWalt 12V battery, the locker circuits can be supported for approximately 3 months, assuming each user unlocks five times a day.

In case of power failure of the DeWalt 12V battery, mechanical override is required to unlock the locker for further actions.

# 7 Troubleshootings

- If the locker turns on but doesn't seem to work properly try recharging the battery.
- If the solenoid stops working when the locker is unlocked try recharging the battery.
- If the locker is blinking red or not turning on when pressing the power button try recharging the battery.
- If the locker is not turning on try pushing in the dewalt battery completely.
- If the solenoid latch is stuck in unlock position, easily tab the solenoid case to reset back to lock position.

# 8 Safety Information

Most of the wires and electronic components are enclosed inside cases. But one portion of a wire that connects to the solenoid may be exposed. Be careful to avoid contacting that wire.

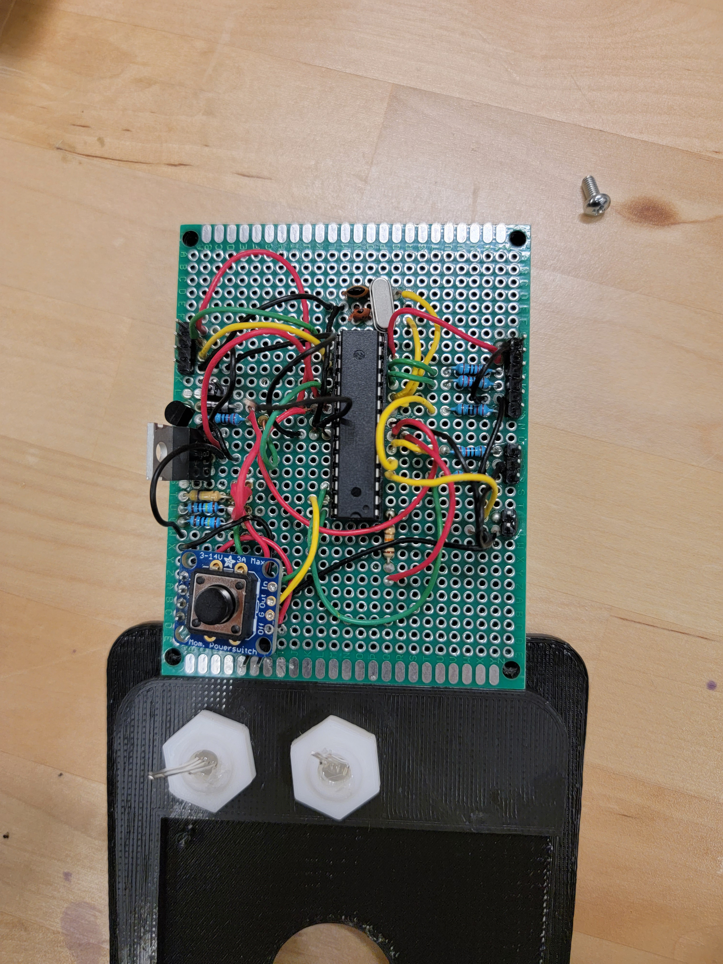
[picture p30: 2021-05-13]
CSE453 Project/Locker Documentation/Images/Assembly Pictures/20210508_151508.jpg

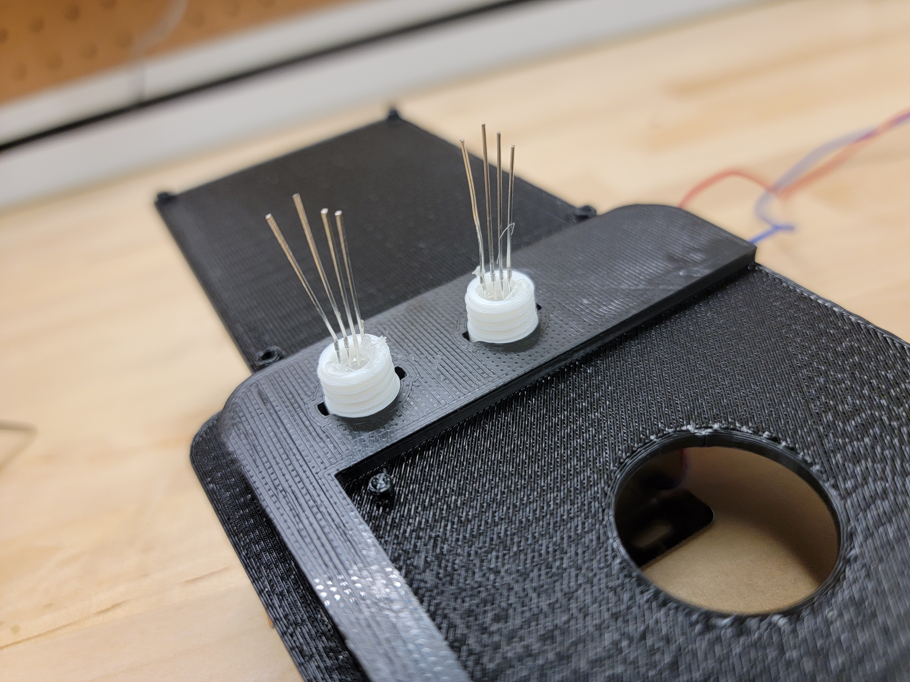
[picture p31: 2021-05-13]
CSE453 Project/Locker Documentation/Images/Assembly Pictures/20210508_150549.jpg

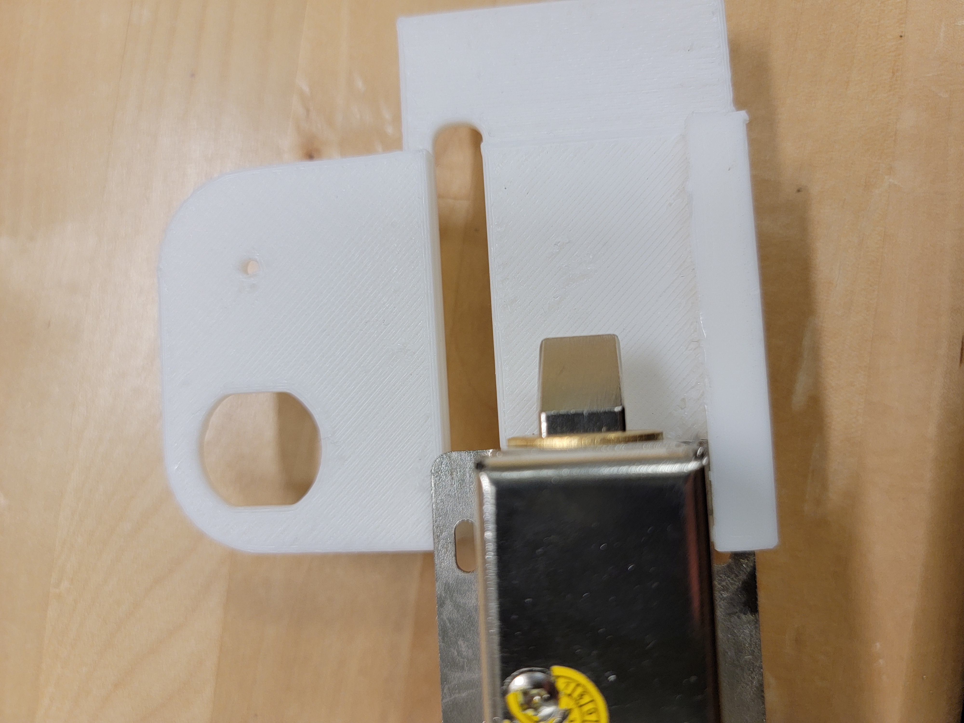
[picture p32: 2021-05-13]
CSE453 Project/Locker Documentation/Images/Assembly Pictures/20210508_160615.jpg

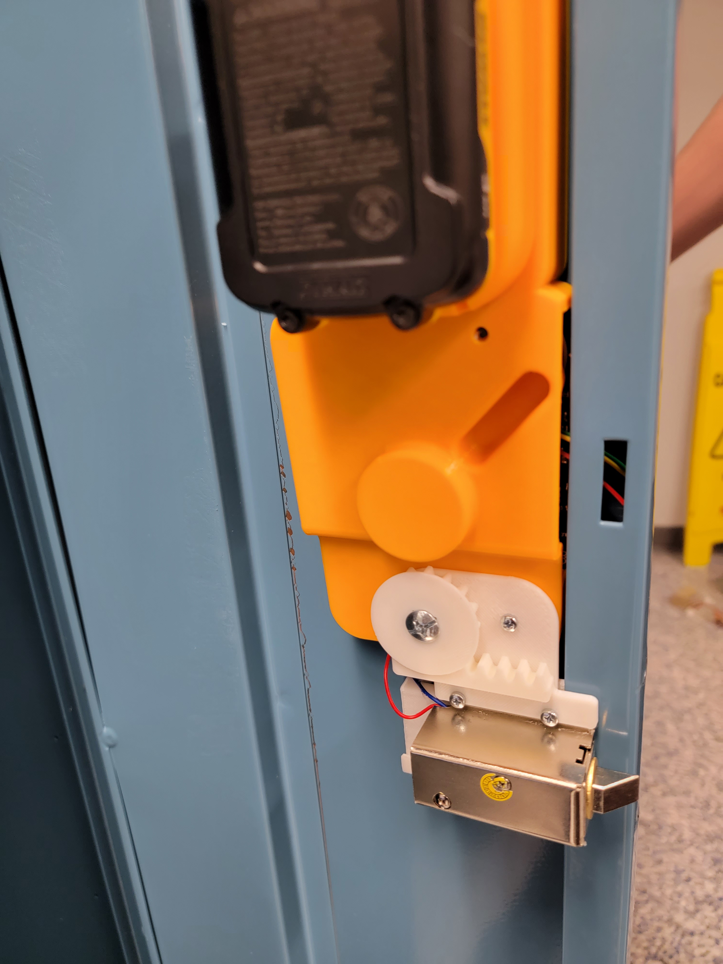
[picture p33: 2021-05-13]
CSE453 Project/Locker Documentation/Images/Assembly Pictures/20210508_185010.jpg

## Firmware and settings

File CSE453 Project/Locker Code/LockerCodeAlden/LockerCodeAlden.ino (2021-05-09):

/*
   Tijmen Van Der Beek
   3/3/2021
   AldenLockerCode
*/
#include <SoftwareSerial.h>
#include <EEPROM.h>

//---------------------------------RFID--------------------------------//
#define RFIDEnablePin 10     //Pin that enables reading. Set as OUTPUT and LOW to read an RFID tag
#define RxPin 11             //Pin to read data from Reader 
#define TxPin 9             //Pin to write data to the Reader NOTE: The reader doesn't get written to, don't connect this line.
#define RFIDSerialRate 2400 //Parallax RFID Reader Serial Port Speed
SoftwareSerial RFIDReader(RxPin, TxPin);

//--------------------------------LEDS---------------------------------//
#define LEDPinR 3
#define LEDPinG 5
#define LEDPinB 6

#define BatteryVoltage A5
#define BatteryLEDR 4
#define BatteryLEDG A3

//LED colors
//Pink: 255, 0, 50
//Orange: 200, 10, 0
//Yellow: 200, 100, 0
//White: 255, 100, 240
//Purple: 60, 0, 200

//-----------------------------OtherOutputs------------------------------//
#define UnlockPin 13
#define Speaker 7
#define TurnOff A4
#define clearButton 2

//--------------------------------Static_Variables-----------------------------//
#define baudrate 9600       //baudrate for the serial moniter
#define tagDelay 1000       //delay between each tag read in ms
#define ERRORBlinkRate 200

//SoundTypes
#define startSound 0
#define unlockSound 1
#define errorSound 2

//address
#define init_address 0
#define master_tag_address 1
#define reg_tag_address 11
#define clear_tag_address 21
#define len_address 31
#define tags_address 32

//tagMatches
#define noMatch -1
#define studentTag 0
#define regTag 1
#define clearTag 2
#define masterTag 3

//other
#define init_num 25 //number is check to see if eeprom is initilized
#define LOCKER_TIME 30 //Time locker has till it turns off in sec
#define UNLOCK_TIME 10 //Time the locker will be unlocked for in sec

//----------------------------Functions----------------------------------//
void ReadSerial(String &ReadTagString);
void clearTags();
void loadTags();
bool writeTag(String data);
int checkTag(String data);
void setLed (int rVal, int gVal, int bVal);
void ledBlink (int rVal, int gVal, int bVal, int halfCycle, int blinkCount);
void soundFeedback(int type);
void initLocker();
void setBatteryLed();
void enableTimerInterrupt();
void resetTimer();

//----------------------------------Variables---------------------------//
String RFIDTAG = ""; //Holds the RFID Code read from a tag

String master_tag = "";
String reg_tag = "";
String clear_tag = "";
String tag_list[32]; //list of student tags

int num_tags = 0;

bool reset = false;
bool locked = true;

int timerCounter = 0;

//---------------------------------Setup--------------------------------//
void setup() {
  // RFID reader SOUT pin connected to Serial RX pin at 2400bps
  RFIDReader.begin(RFIDSerialRate);

  // Set Enable pin as OUTPUT to connect it to the RFID /ENABLE pin
  pinMode(RFIDEnablePin, OUTPUT);
  pinMode(UnlockPin, OUTPUT);
  pinMode(Speaker, OUTPUT);
  pinMode(TurnOff, OUTPUT);
  pinMode(clearButton, INPUT_PULLUP);

  pinMode(BatteryVoltage, INPUT);
  pinMode(BatteryLEDR, OUTPUT);
  pinMode(BatteryLEDG, OUTPUT);

  // Activate the RFID reader
  // Setting the RFIDEnablePin HIGH will deactivate the reader
  // which could be usefull if you wanted to save battery life for
  // example.
  digitalWrite(RFIDEnablePin, LOW);
  digitalWrite(TurnOff, LOW);

  // sets baudrate for serial moniter
  Serial.begin(baudrate);

  //sets Interrupts
  attachInterrupt(digitalPinToInterrupt(clearButton), resetISR, FALLING);

  interrupts();

  setBatteryLed(); //setsBatteryLED
  
  enableTimerInterrupt(); //sets timer interrupt for auto shut off
  
  //loads all registered tags
  loadTags();
  Serial.println("Setup done!");

  soundFeedback(startSound);
  
  setLed(255, 0, 0);//LED Red
}


//---------------------------------Loop--------------------------------//
void loop() {

  //If tag is being read
  if (RFIDReader.available() > 0) // If data available from reader
  {
    setLed(255, 80, 0); //LED Yellow

    digitalWrite(RFIDEnablePin, HIGH);
    ReadSerial(RFIDTAG);  //Read the tag number from the reader. Should return a 10 digit serial number

    //checks if tag is in list
    int tagMatch = checkTag(RFIDTAG);

    //adds tag if in add tag mode
    //else unlocks if tag is registered
    if (tagMatch == regTag) {
      setLed(0, 0, 255); //sets Led to blue
      
      digitalWrite(RFIDEnablePin, LOW);
      while(RFIDReader.available() <= 0){}
      digitalWrite(RFIDEnablePin, HIGH);
      ReadSerial(RFIDTAG);

      tagMatch = checkTag(RFIDTAG);
      
      if(tagMatch == noMatch || tagMatch == studentTag){
        writeTag(RFIDTAG);
        delay(tagDelay - 400);
        ledBlink(0, 0, 255, ERRORBlinkRate, 3 + tagMatch); //blinks blue for registering tag. (blinks 3 times if already registered 2 if not registered yet)
      }else{
        delay(tagDelay - 400);
        ledBlink(255, 0, 0, ERRORBlinkRate, 2); //blinks red for already registered tag
        switch(tagMatch){
          case regTag:
            ledBlink(0, 0, 255, ERRORBlinkRate, 1);
            break;
          case clearTag:
            ledBlink(255, 0, 50, ERRORBlinkRate, 1);
            break;
          case masterTag:
            ledBlink(255, 100, 240, ERRORBlinkRate, 1);
            break;
        }
      }
      digitalWrite(RFIDEnablePin, LOW);

    } else if (tagMatch == clearTag) {
      clearTags();
      delay(tagDelay - 400);
      ledBlink(255, 0, 50, ERRORBlinkRate, 2); //blinks pink for clear
      
      digitalWrite(RFIDEnablePin, LOW);
      
    } else if (tagMatch == studentTag || tagMatch == masterTag) { //unlocks locker
      delay(tagDelay - 400);
      soundFeedback(unlockSound);

      //unlock
      digitalWrite(UnlockPin, HIGH);
      timerCounter = UNLOCK_TIME; //sets timer to unlock_time

      ledBlink(0, 255, 0, ERRORBlinkRate, 2); //blinks green for unlocking tag
      locked = false;

    } else{
      delay(tagDelay - 600);
      soundFeedback(errorSound);
      ledBlink(255, 0, 0, ERRORBlinkRate, 3); //blinks red for wrong tag

      digitalWrite(RFIDEnablePin, LOW);
    }

    setLed(locked * 255, !locked * 255, 0); //sets led to locker state
  }

  //if reset button was pushed
  if (reset == true) {
    ledBlink(60, 0, 200, ERRORBlinkRate, 2); //blinks purple for reset
    resetLocker();
    reset = false;

    setLed(locked * 255, !locked * 255, 0); //sets led to locker state
  }
}

//---------------------------------Functions--------------------------------//
/*
   ReadSerial
    This function reads the tag infront of the RFID sensor and returns the string in the through the passed in string
    Inputs:
    String RFIDTAG
*/
void ReadSerial(String &ReadTagString)
{
  resetTimer();//resets timer when ever readSerial is run
  
  int bytesread = 0;
  int  val = 0;
  char code[10];
  String TagCode = "";

  if (RFIDReader.available() > 0) {         // If data available from reader
    if ((val = RFIDReader.read()) == 10) {  // Check for header
      bytesread = 0;
      while (bytesread < 10) {              // Read 10 digit code
        if ( RFIDReader.available() > 0) {
          val = RFIDReader.read();
          if ((val == 10) || (val == 13)) { // If header or stop bytes before the 10 digit reading
            break;                         // Stop reading
          }
          code[bytesread] = val;           // Add the digit
          bytesread++;                     // Ready to read next digit
        }
      }
      if (bytesread == 10) {               // If 10 digit read is complete

        for (int x = 0; x < 10; x++)       //Copy the Chars to a String
        {
          TagCode += code[x];
        }
        ReadTagString = TagCode;          //Update the caller

        delay(500);                       //adds delay for double scan
        while (RFIDReader.available() > 0) //Burn off any characters still in the buffer
        {
          RFIDReader.read();
        }

      }
      bytesread = 0;
      TagCode = "";
    }
  }
}

/*
   clearTags
   This function clears all the tags in memory
*/
void clearTags() {
  EEPROM.write(len_address, 0);
  num_tags = 0;
}

/*
  resetLocker
  This function resets the locker
*/
void resetLocker(){
  EEPROM.write(init_address, 0);
  digitalWrite(TurnOff, HIGH);
}

/*
   loadTags
   This function loads all the tags. student tags go into the global tag_list. Init num is a number to check if the program has been initilized before
*/
void loadTags() {
  //checks init num
  if(EEPROM.read(init_address) != init_num){
    initLocker();
  }
  
  String tempStr = "";
  int strIndex;
  int strEnd;
  
  //loads master tag
  strIndex = master_tag_address;
  strEnd = strIndex + 10;
  for (strIndex; strIndex < strEnd; strIndex++) {
    tempStr += (char) EEPROM.read(strIndex);
  }
  master_tag = tempStr;
  tempStr = "";

  //loads register tag
  strIndex = reg_tag_address;
  strEnd = strIndex + 10;
  for (strIndex; strIndex < strEnd; strIndex++) {
    tempStr += (char) EEPROM.read(strIndex);
  }
  reg_tag = tempStr;
  tempStr = "";

  //loads clear tag
  strIndex = clear_tag_address;
  strEnd = strIndex + 10;
  for (strIndex; strIndex < strEnd; strIndex++) {
    tempStr += (char) EEPROM.read(strIndex);
  }
  clear_tag = tempStr;
  tempStr = "";

  //loads student tags
  num_tags = EEPROM.read(len_address);

  for (int i = 0; i < num_tags; i++) {
    strIndex = tags_address + (i * 10);
    strEnd = strIndex + 10;
    for (strIndex; strIndex < strEnd; strIndex++) {
      tempStr += (char) EEPROM.read(strIndex);
    }
    tag_list[i] = tempStr;
    tempStr = "";
  }
}

/*
  initLocker
  This function puts the locker in initilize mode mode if it hasn't been initilized before.
  In initilize mode the locker will blink white for when it wants a master tag to be registered, blue for the register tag and pink for the clear tag. Once 3 tags have been initlized it will exit and run as normal.
*/
void initLocker() {
  //register master tag
  setLed(255, 100, 240);
   while(master_tag == ""){
    if (RFIDReader.available() > 0) // If data available from reader
    {
      setLed(255, 80, 0); //LED Yellow
      digitalWrite(RFIDEnablePin, HIGH);
      ReadSerial(RFIDTAG);  //Read the tag number from the reader. Should return a 10 digit serial number
  
      //checks if tag is in list
      int isTagReg = checkTag(RFIDTAG);
      Serial.println(isTagReg);
  
      //adds tag if in add tag mode
      //else uunlocks if tag is registered
      if (isTagReg == -1) {
          master_tag = RFIDTAG;
          
          int start_address = master_tag_address;
          int end_address = master_tag_address + 10;
          for (int i = start_address; i < end_address; i++) {
            EEPROM.write(i, RFIDTAG[i - start_address]);
          }
          
          soundFeedback(unlockSound);
          ledBlink(0, 255, 0, ERRORBlinkRate, 2);
          digitalWrite(RFIDEnablePin, LOW);
      }else {
          soundFeedback(errorSound);
          ledBlink(255, 0, 0, ERRORBlinkRate, 2);
          setLed(255, 100, 240);
          digitalWrite(RFIDEnablePin, LOW);
      }
    }
  }

  //register register tag
  setLed(0, 0, 255);
  while(reg_tag == ""){
    if (RFIDReader.available() > 0) // If data available from reader
    {
      setLed(255, 80, 0); //LED Yellow
      digitalWrite(RFIDEnablePin, HIGH);
      ReadSerial(RFIDTAG);  //Read the tag number from the reader. Should return a 10 digit serial number
  
      //checks if tag is in list
      int isTagReg = checkTag(RFIDTAG);
      Serial.println(isTagReg);
  
      //adds tag if in add tag mode
      //else uunlocks if tag is registered
      if (isTagReg == -1) {
          reg_tag = RFIDTAG;
          
          int start_address = reg_tag_address;
          int end_address = reg_tag_address + 10;
          for (int i = start_address; i < end_address; i++) {
            EEPROM.write(i, RFIDTAG[i - start_address]);
          }
          
          soundFeedback(unlockSound);
          ledBlink(0, 255, 0, ERRORBlinkRate, 2);
          digitalWrite(RFIDEnablePin, LOW);
      }else {
          soundFeedback(errorSound);
          ledBlink(255, 0, 0, ERRORBlinkRate, 2);
          setLed(0, 0, 255);
          digitalWrite(RFIDEnablePin, LOW);
      }
    }
  }

  //register clear tag
  setLed(255, 0, 50);
  while(clear_tag == ""){
    if (RFIDReader.available() > 0) // If data available from reader
    {
      setLed(255, 80, 0); //LED Yellow
      digitalWrite(RFIDEnablePin, HIGH);
      ReadSerial(RFIDTAG);  //Read the tag number from the reader. Should return a 10 digit serial number
  
      //checks if tag is in list
      int isTagReg = checkTag(RFIDTAG);
      Serial.println(isTagReg);
  
      //adds tag if in add tag mode
      //else uunlocks if tag is registered
      if (isTagReg == -1) {
          clear_tag = RFIDTAG;
          
          int start_address = clear_tag_address;
          int end_address = clear_tag_address + 10;
          for (int i = start_address; i < end_address; i++) {
            EEPROM.write(i, RFIDTAG[i - start_address]);
          }
          
          soundFeedback(unlockSound);
          ledBlink(0, 255, 0, ERRORBlinkRate, 2);
          digitalWrite(RFIDEnablePin, LOW);
      }else {
          soundFeedback(errorSound);
          ledBlink(255, 0, 0, ERRORBlinkRate, 2);
          setLed(255, 0, 50);
          digitalWrite(RFIDEnablePin, LOW);
      }
    }
  }
  //initilizes number of student tags
  EEPROM.write(len_address, 0);

  //sets init_num in eepron
  EEPROM.write(init_address, init_num);
}

/*
   writeTag
   This function adds a tag to memory and returns true if succsesful and false if reached max tags
   Inputs:
   String tag
   Returns:
   bool sucsess
*/
bool writeTag(String data) {
  if (num_tags == 32) {
    return false;
  }
  int start_address = (num_tags * 10) + tags_address;
  int end_address = start_address + 10;
  for (int i = start_address; i < end_address; i++) {
    EEPROM.write(i, data[i - start_address]);
  }

  tag_list[num_tags] = data;
  num_tags++;
  EEPROM.write(len_address, num_tags);

  return true;
}

/*
   checkTag
   checks the given tag with the registered tags if any of them match it returns true.
   Inputs:
   String tag
   Returns:
   int -1 no match
   int 0 student tag
   int 1 reg_tag
   int 2 clear_Tag
   int 4 master tag
*/
int checkTag(String data) {
  if(data == master_tag){
    return masterTag;
  }else if(data == reg_tag){
    return regTag;
  }else if(data == clear_tag){
    return clearTag;
  }
  for (int i = 0; i < num_tags; i++) {
    if (data == tag_list[i]) {
      return studentTag;
    }
  }
  return noMatch;
}

/*
   setLed
   sets the rgb led color
   Input:
   int red value (0-255)
   int green value (0-255)
   int blue value (0-255)
*/
void setLed (int rVal, int gVal, int bVal) {
  analogWrite (LEDPinR, rVal);
  analogWrite (LEDPinG, gVal);
  analogWrite (LEDPinB, bVal);
}

/*
   ledBlink
   Blink the RGB LED given the provided RGB value, the time for each half cycle (time off, time on, in ms) and the number of blinks
   Input:
   int red value (0-255)
   int green value (0-255)
   int blue value (0-255)
   int halfCycle (ms)
   int blinkCount
*/
void ledBlink (int rVal, int gVal, int bVal, int halfCycle, int blinkCount) {
  for (int i = 0; i < blinkCount; i++) {
    setLed(0, 0, 0);
    delay(halfCycle);
    setLed(rVal, gVal, bVal);
    delay(halfCycle);
  }
}

/*
   soundFeedback
   adds sound effects to the locker for better feed back
   Input:
   int type (0 start, 1 unlock, 2 wrong tag)
*/
void soundFeedback(int type) {
  switch (type) {
    case 0:
      tone(Speaker, 100, 200);
      delay(200);
      tone(Speaker, 300, 200);
      delay(200);
      tone(Speaker, 400, 200);
      delay(200);
      break;
    case 1:
      tone(Speaker, 300, 200);
      delay(200);
      tone(Speaker, 400, 200);
      delay(200);
      break;
    case 2:
      tone(Speaker, 100, 200);
      delay(200);
      tone(Speaker, 50, 200);
      delay(200);
      break;
  }
}

/*
  setBatteryLed
  sets the battery led color based on the voltage of the battery
 */
void setBatteryLed(){
  int batteryVoltage = analogRead(BatteryVoltage);
  Serial.print("BatteryVoltage:"); 
  Serial.println(batteryVoltage);
  
  if(batteryVoltage >= 690){
    analogWrite(BatteryLEDR, 0);
    analogWrite(BatteryLEDG, 255);
    
  }else if(batteryVoltage >= 630){
    analogWrite(BatteryLEDR, 255);
    analogWrite(BatteryLEDG, 0);
    
  }else{
    analogWrite(BatteryLEDR, 255);
    analogWrite(BatteryLEDG, 0);
    ledBlink(255, 0, 0, ERRORBlinkRate, 3);
    digitalWrite(TurnOff, HIGH);
  }
}

/*
 * Sets the timer interrupt to interrupt every second
 */
 void enableTimerInterrupt(){
    cli();//disables interrupts
    timerCounter = LOCKER_TIME;
    
    
    //setting Timer1 register to 0
    TCCR1A = 0;
    TCCR1B = 0;
    //initilizing the counter to 0
    TCNT1  = 0;
    //setting cmp match number
    OCR1A = 15624; // = (16*10^6) / (1*1024) - 1 (must be <65536)
    //turn on CTC mode
    TCCR1B |= (1 << WGM12);
    //setting prescaler
    TCCR1B |= (1 << CS12) | (1 << CS10);
    //enable timer compare interrupt
    TIMSK1 |= (1 << OCIE1A);
    
    sei();//enable interrupts
 }

/*
 * resets the timer back to Locker_Time when ever called
 */
void resetTimer(){
    cli();//disables interrupts
    TCNT1 = 0; //reset counter to 0
    timerCounter = LOCKER_TIME;
    sei();//enable interrupts
}

//---------------------------------Interrupts--------------------------------//
/*
   resetISR
   resets entire locker
*/
void resetISR() {
  delay(5);
  if(digitalRead(clearButton) == 0){
    reset = true;
    setLed(70, 0, 200);
  }
}

/*
 * Turns off locker after timer interrupt activates
 */
 ISR(TIMER1_COMPA_vect){
  if(timerCounter == 0){
    digitalWrite(TurnOff, HIGH);
  }
  timerCounter--;
  Serial.print("Timer: ");
  Serial.println(timerCounter);
 }
 

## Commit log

2021-05-09 Uploading the fritizing file along with its png file
    [Locker Circuit Schematic.fzz]
2021-05-09 Uploading all the files
    [ButtonNut.stl, Case_Back.stl, Case_Front.stl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]
2021-05-13 Added all the files
    [Locker Circuit Schematic.fzz, SolenoidRack(L).stl]
2021-05-14 added assembly guide
